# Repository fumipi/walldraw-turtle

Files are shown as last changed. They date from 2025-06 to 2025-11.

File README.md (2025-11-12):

[English version → README_en.md](./README_en.md)
# 🐢かめプロッター

Raspberry Pi Pico と MicroPython で作る最小構成の亀の形をした垂直型ペンプロッターです。  
CSVファイルに基づいて線画を描きます。

---

## プロジェクト概要

### **ハードウェア & ファームウェア ** 
- タートルグラフィックス風の MicroPython 制御コード  
- **Raspberry Pi Pico**, **28BYJ-48 ステッピングモータ ×2**, **SG90 サーボモータ ×1** を使用  
- 電源は USB から給電 
- **3Dプリント部品（STL）**、**回路図**、**サンプル CSV**   

## 使い方

### **タートルプロッターのセットアップ**
1. STLフォルダの亀パーツを3Dプリントする
2. Schematicフォルダにある回路図を参考に配線する
3. [Thonny IDE](https://thonny.org/) をインストール  
4. Raspberry Pi Pico を USB で PC に接続、MicroPythonをインストール [参考](https://www.raspberrypi.com/documentation/microcontrollers/micropython.html)
5. Codeフォルダにあるコードを全てPicoにDrag & Drop
6. `turtle_plotter/code/main.py` を Thonny で開いて実行  
5. `points.csv` を Pico にアップロード（省略可）

**動作モード**
- `points.csv` がある場合 → CSV 座標を描画  
- ない場合 → `main.py` 内の `test_drawing` に従って 100mm 四方のテスト描画  

---

### 線描データ作成アプリ
[https://vectorizer.streamlit.app/](https://vectorizer.streamlit.app/) にアクセスし、画像や をアップロード。  
生成された CSV をダウンロードして `points.csv` として Pico に保存します。
**主な機能**
- 輪郭抽出・センターライン抽出  
- 経路の最適化と単純化  
- 画像 → CSV変換  （このプロッターでは使いませんが、SVGやGコードへの変換もできます）

## より詳しい作り方
[note](https://note.com/fumi_note/n/n50b205639b7f)をご覧ください。

## 参考プロジェクト
- 参考: [Make a Raspberry Pi Pico pen plotter](https://www.raspberrypi.com/news/make-a-raspberry-pi-pico-pen-plotter/)

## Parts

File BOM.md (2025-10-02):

###Electronics
1 Raspberry Pi Pico
1 SG90 servo motor
2 28BYJ-48 stepper motors
2 ULN2003 motor driver boards
1 Half breadboard

###Hardware
1 Whiteboard 30cm x 40cm
1 Whiteboard marker
1 turtle_buttom (3d print)
1 turtle_cover (3d print)
2 motor mount (3d print)
2 spur (3d print)ß
1 weghts (3d print)
4 o 5 coins for weightsß

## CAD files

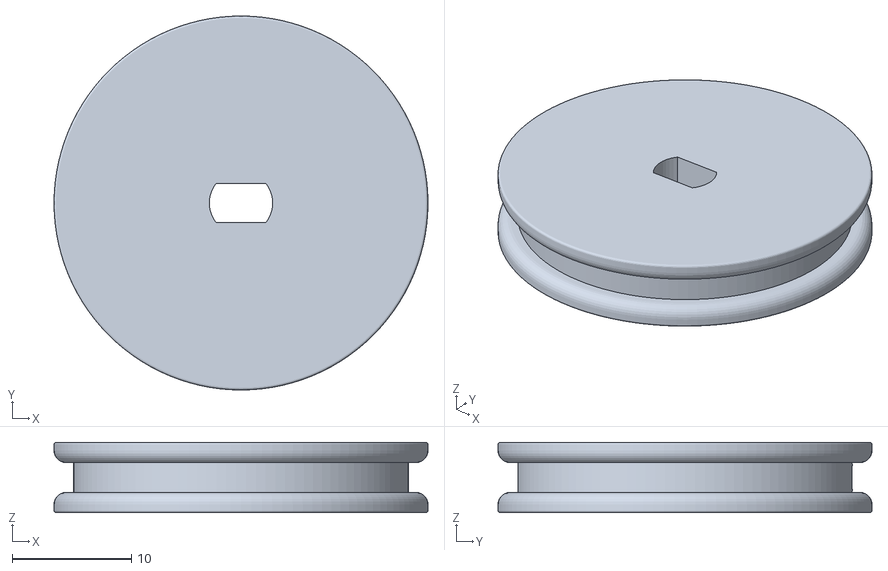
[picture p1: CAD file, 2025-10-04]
stl/spur.stl
31.3 x 31.3 x 5.90

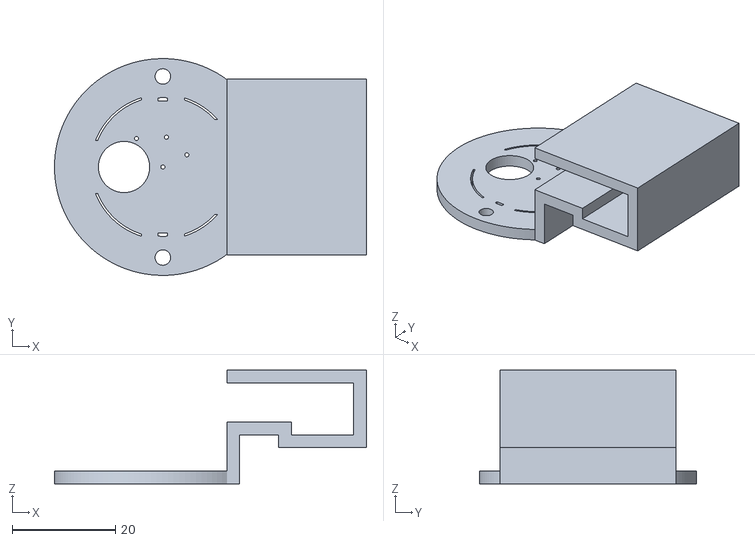
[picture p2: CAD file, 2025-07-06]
stl/motor_mount.stl
60.3 x 41.9 x 22.0

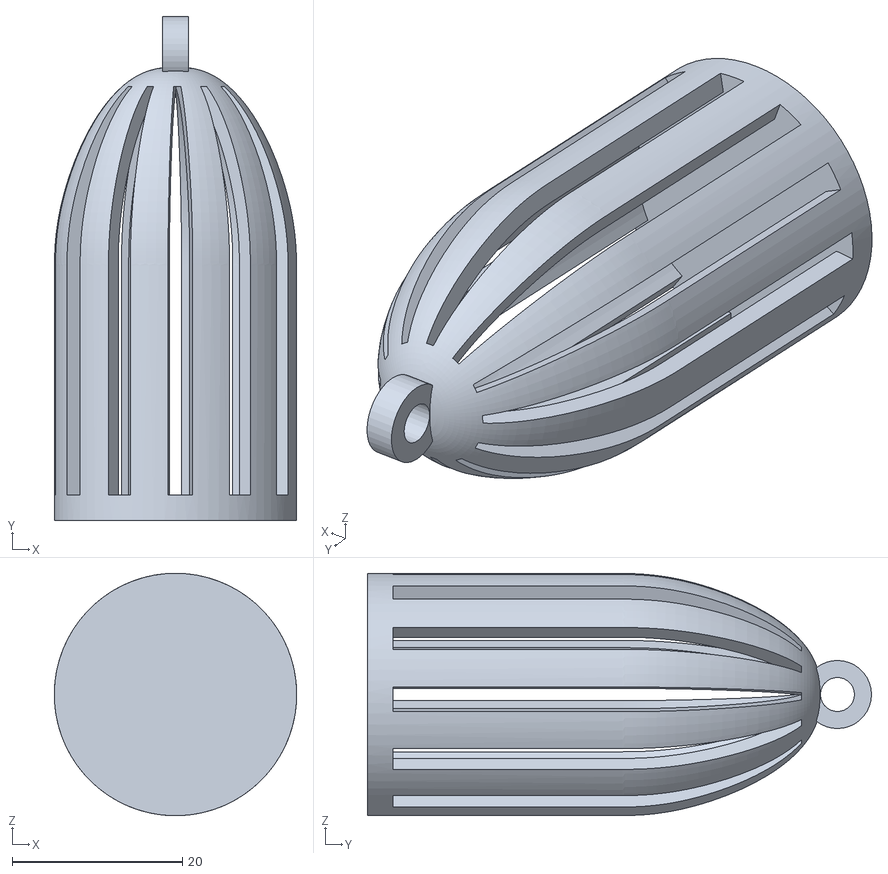
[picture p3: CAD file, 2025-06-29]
stl/weight.stl
28.5 x 59.2 x 28.5

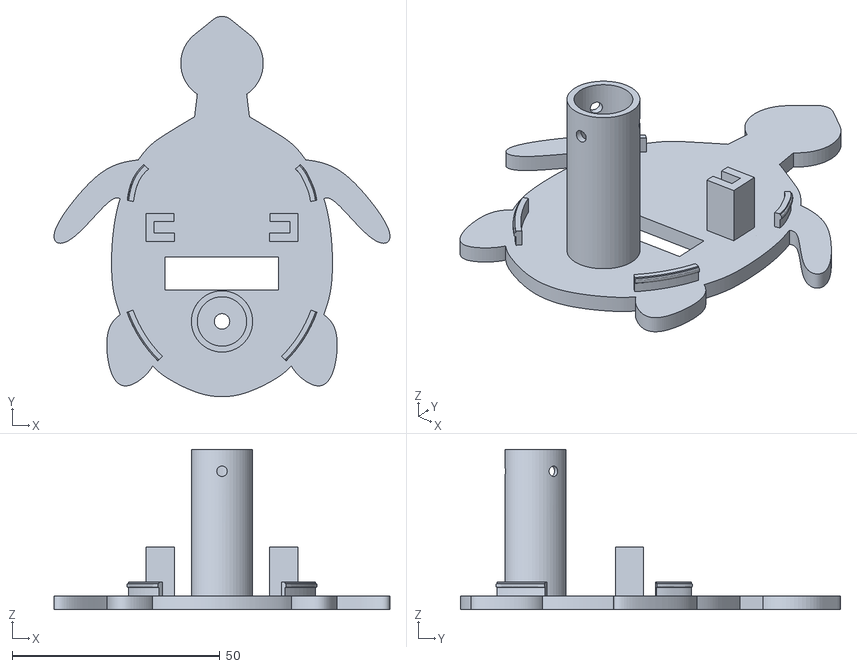
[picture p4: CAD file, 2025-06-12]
stl/turtle_bottom.stl
80.8 x 91.5 x 38.5

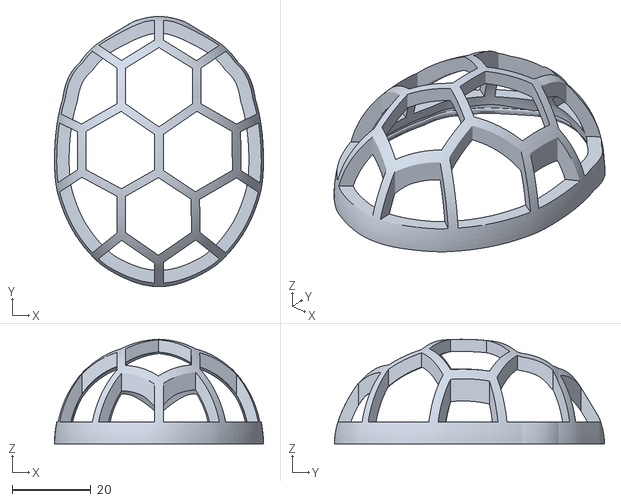
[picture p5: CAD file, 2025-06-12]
stl/turtle_cover.stl
53.1 x 68.6 x 26.6

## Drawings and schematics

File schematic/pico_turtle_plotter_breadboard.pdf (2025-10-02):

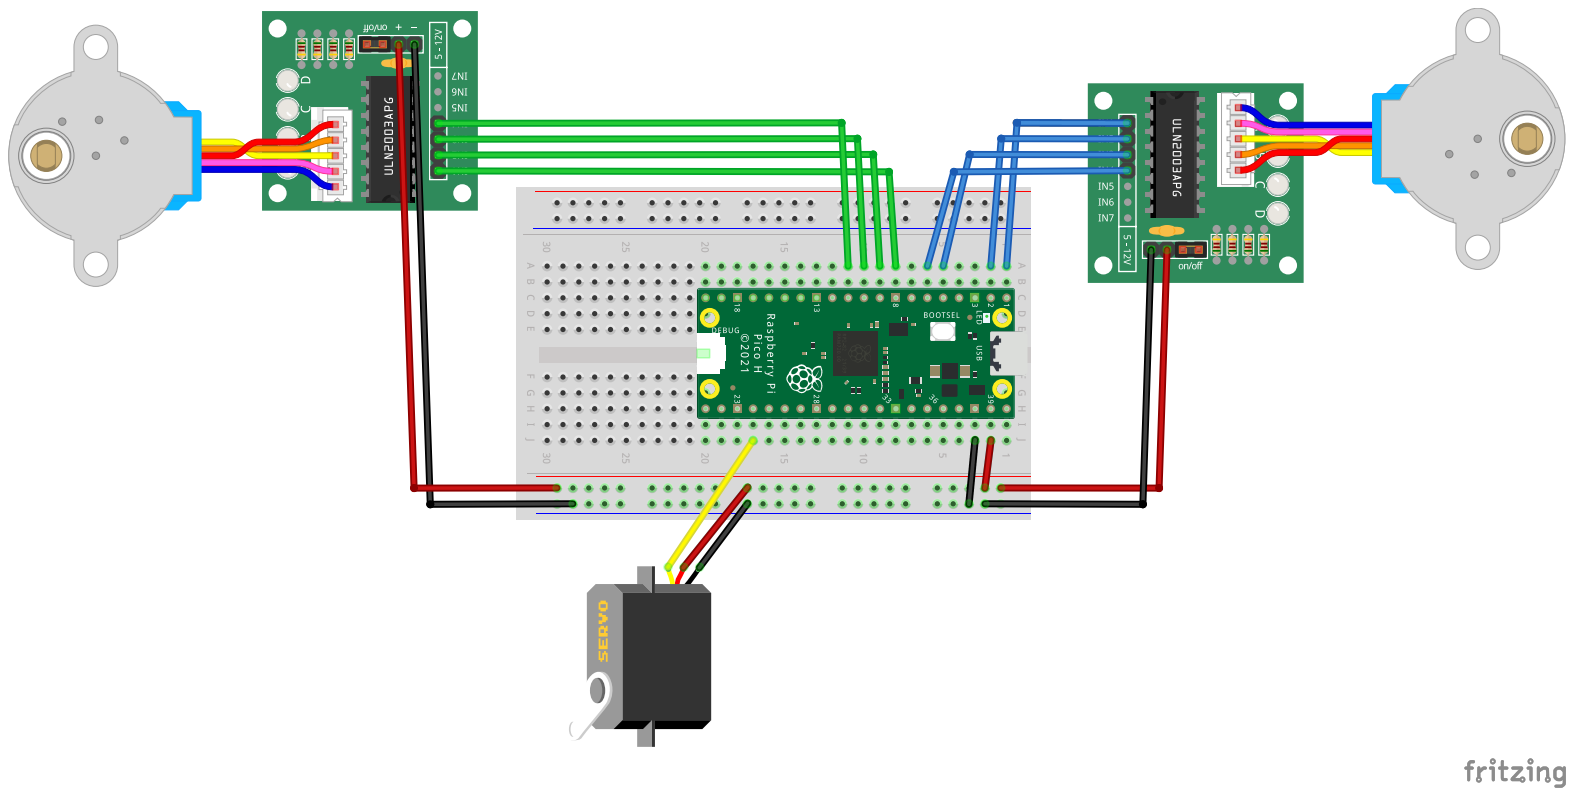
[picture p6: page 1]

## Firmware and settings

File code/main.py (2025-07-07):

from machine import Pin
import time
import os
from config import *
from plotter import WallPlotter

def main():
    # Initialize plotter
    plotter = WallPlotter()
    plotter.init()
    
    print("Wall Drawing Plotter - CSV File Reader")
    print("Starting drawing process...")
    
    # Test drawing pattern - you can modify these coordinates freely
    # Default: 100mm x 100mm square pattern (useful for calibration)
    test_drawing = [
        (50.0, 0.0), (50.0, 50.0), (0.0, 50.0), (-50.0, 50.0),
        (-50.0, 0.0), (-50.0, -50.0), (0.0, -50.0), (50.0, -50.0),
        (50.0, 0.0),(0.0,0.0)
    ]
    
    # Check if points.csv exists
    try:
        os.stat("points.csv")
        file_exists = True
        print("points.csv found. Starting drawing process.")
    except:
        file_exists = False
        print("points.csv not found. Drawing test square for calibration.")
    
    # Start drawing
    print("Starting to draw")
    # First make sure pen is up
    plotter.pen_up()
    time.sleep(1)
    
    if file_exists:
        # Process the CSV file
        success = plotter.read_csv_and_plot("points.csv")
    else:
        # Draw the test drawing
        print("Drawing test pattern...")
        # Move to first point with pen up
        plotter.pen_up()
        time.sleep(0.5)
        plotter.goto(test_drawing[0][0], test_drawing[0][1])
        
        # Draw the pattern
        plotter.pen_down()
        time.sleep(0.5)
        for x, y in test_drawing[1:]:
            plotter.goto(x, y)
        
        success = True
    
    if success:
        print("Drawing completed successfully!")
    else:
        print("Error occurred during drawing.")
    
    # Return pen to up position when done
    plotter.pen_up()
    print("Program execution complete")

if __name__ == "__main__":
    main() 

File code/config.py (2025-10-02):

# Configuration for Wall Drawing Plotter

# Hardware pins
M1_PIN1 = 6
M1_PIN2 = 7
M1_PIN3 = 8
M1_PIN4 = 9
M2_PIN1 = 0
M2_PIN2 = 1
M2_PIN3 = 3
M2_PIN4 = 4
SERVO_PIN = 18

# Drawing area configuration
START_X = 0
START_Y = 0
X_SEPARATION = 250  # x cm apart motors
X_MAX_POS = X_SEPARATION * 0.5  
X_MIN_POS = -X_SEPARATION * 0.5  
Y_MAX_POS = -200 # Bottom of drawing area 
Y_MIN_POS = 200  # Top of drawing area 

# Pen servo configuration
PEN_UP_ANGLE = 110
PEN_DOWN_ANGLE = 50

# Motor configuration
INVERT_M1_DIR = 1  
INVERT_M2_DIR = -1
STEPS_PER_TURN = 2048  # 28BYJ-48 stepper motor (with gear reduction)
SPOOL_DIAMETER = 28    # mm
SPOOL_CIRC = SPOOL_DIAMETER * 3.1416  # Line spool circumference
DEFAULT_XY_MM_PER_STEP = SPOOL_CIRC / STEPS_PER_TURN  # Min step resolution

# Motor speeds
STEPS_PER_SEC = 600

# Axes definitions
X_AXIS = 0
Y_AXIS = 1 

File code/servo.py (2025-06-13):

from machine import Pin, PWM
import time

class SimpleServo:
    """A simplified servo motor control library.
    This is a basic implementation that provides simple angle control (0-180 degrees)
    using PWM signals. It lacks advanced features like speed control, position feedback,
    and calibration support that are common in more comprehensive servo libraries.
    """
    
    def __init__(self, pin_num):
        """Initialize servo on the specified pin"""
        self.pwm = PWM(Pin(pin_num))
        self.pwm.freq(50)  # Standard 50Hz for servos
        self.min_duty = 1000  # Minimum duty cycle (0 degrees)
        self.max_duty = 9000  # Maximum duty cycle (180 degrees)
        self.current_angle = 0
        
    def attach(self, pin_num=None):
        """Attach the servo (or reattach to a new pin)"""
        if pin_num is not None:
            self.pwm = PWM(Pin(pin_num))
            self.pwm.freq(50)
        
    def detach(self):
        """Detach the servo"""
        self.pwm.deinit()
        
    def write(self, angle):
        """Set the servo to the specified angle (0-180 degrees)"""
        if angle < 0:
            angle = 0
        elif angle > 180:
            angle = 180
            
        # Convert angle to duty cycle
        duty = int(self.min_duty + (self.max_duty - self.min_duty) * angle / 180)
        self.pwm.duty_u16(duty)
        self.current_angle = angle
        
    def read(self):
        """Return the current angle"""
        return self.current_angle 

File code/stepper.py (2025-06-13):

from machine import Pin
import time
import math
from config import *

class SimpleStepper:
    """A simplified stepper motor control library for 28BYJ-48 stepper motors.
    This is a basic implementation that provides constant speed movement without acceleration.
    """
    
    # Full step sequence for 28BYJ-48
    STEP_SEQUENCE = [
        [1, 1, 0, 0],  # A+B
        [0, 1, 1, 0],  # B+C
        [0, 0, 1, 1],  # C+D
        [1, 0, 0, 1],  # D+A
]
    
    def __init__(self):
        self.pins = [None, None, None, None]
        self.position = 0
        self.current_step = 0
        self.steps_per_second = 1000
        
    def connect_to_pins(self, pin1, pin2, pin3, pin4):
        """Connect the stepper to the specified pins"""
        self.pins[0] = Pin(pin1, Pin.OUT)
        self.pins[1] = Pin(pin2, Pin.OUT)
        self.pins[2] = Pin(pin3, Pin.OUT)
        self.pins[3] = Pin(pin4, Pin.OUT)
        
        # Initialize pins to 0
        for pin in self.pins:
            pin.value(0)
            
    def set_speed_in_steps_per_second(self, steps_per_second):
        """Set the stepper speed in steps per second"""
        self.steps_per_second = steps_per_second
        
    def step(self, direction):
        """Move one step in the specified direction (1 or -1)"""
        # Update current step based on direction
        self.current_step = (self.current_step + direction) % 4
        
        # Set pins according to sequence
        for i in range(4):
            self.pins[i].value(self.STEP_SEQUENCE[self.current_step][i])
        
        # Update position
        self.position += direction
        
        # Delay to maintain speed (simplified - no acceleration)
        time.sleep(1 / self.steps_per_second)
        
    def move_relative_in_steps(self, steps):
        """Move relative number of steps (can be positive or negative)"""
        direction = 1 if steps > 0 else -1
        steps = abs(steps)
        
        for _ in range(steps):
            self.step(direction)
            
    def get_position(self):
        """Return the current position in steps"""
        return self.position 
    
    def disable_motor(self):
        for pin in self.pins:
            pin.value(0)
    

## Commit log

2025-06-02 add new version
    [points.csv, points_cross.csv, points_svg_icon.csv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]
2025-06-12 Create streamlit app
    [curvey-body.amf, gondola-v3__repaired.stl, motor_mount.stl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]
2025-06-13 Simplified codes
    [points.csv]
2025-06-13 improved the moveto function and delete all other non-working versions
    [points.csv, points_cross.csv, points_svg_icon.csv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]
2025-06-13 Latest working version
    [points.csv]
2025-06-29 streamlit app to convert image to vector
    [chojugiga.csv, motor_mount.stl, points.csv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]
2025-07-02 simplified app_v2.py
    [chojugiga_2mm.csv, stackchan_birthday.csv]
2025-07-06 new file structure
    [chojugiga.csv, chojugiga_2mm.csv, motor_mount.stl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]
2025-07-06 Reorganized file structure and add more explanations
    [chojugiga.csv, choujugiga.csv, motor_mount.stl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]
2025-07-06 commit before changing vectorizer_app.py
    [points.csv]
2025-07-07 improved streamlit app
    [points.csv, weight.3mf]
2025-07-16 create 2nd version of vectorizer app
    [elephantbypicasso.csv, points.csv, stackchan_birthday.csv]
2025-10-02 update spur model
    [elephantbypicasso.csv, picasso_elephant.csv, pico_turtle_plotter.fzz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]
2025-10-02 update servo pin position
    [pico_turtle_plotter.fzz]
